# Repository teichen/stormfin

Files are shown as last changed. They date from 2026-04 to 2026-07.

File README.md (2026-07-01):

# StormFin
underactuated fish finder

# ChibbComm
raspberry pi land communicator and StormFin controller

## motivation
avoiding $1500+ Garbin LiveScope Plus \
avoiding $2000+ per acoustic modem \
current state of the art is forward facing sonar \
steerable transducer on trolling motor, 20 deg sonar beam, 100 ft range \
proposal - AUV tracking

## StormFin microcontroller and comms
Adafruit METRO 328 / Arduino Nano Complementary Filtering on-board \
Embedded EKF would require STM32H7 (for example), CMSIS-DSP library, etc. \
Arduino Due (84MHz 32-bit ARM Cortex-M3 processor, 96KB SRAM) would struggle with EKF \
Acoustic modem (design described below)

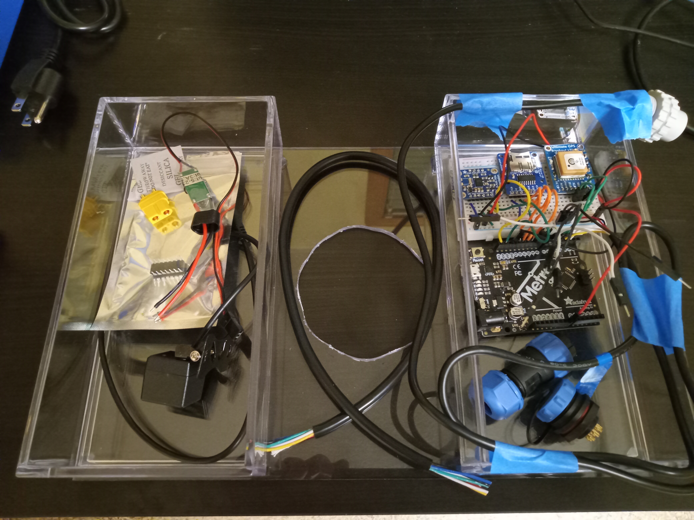
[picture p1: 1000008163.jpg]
prototyping1

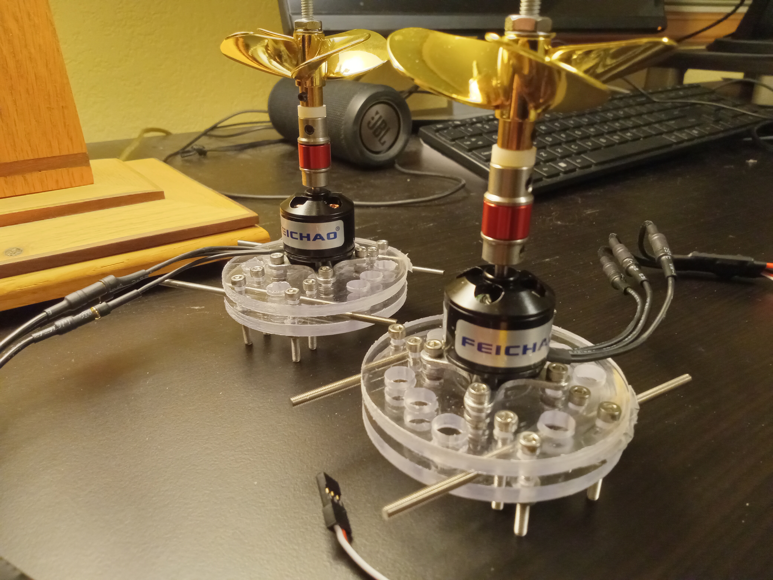
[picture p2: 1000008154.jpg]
prototyping0


## ChibComm microcontroller and comms
Raspberry Pi (3) Model B+ \
WhatsApp for communication with shoreline \
Acoustic modem (design described below) \
GNU Radio for signal processing (freq shift keying and phase shift keying)

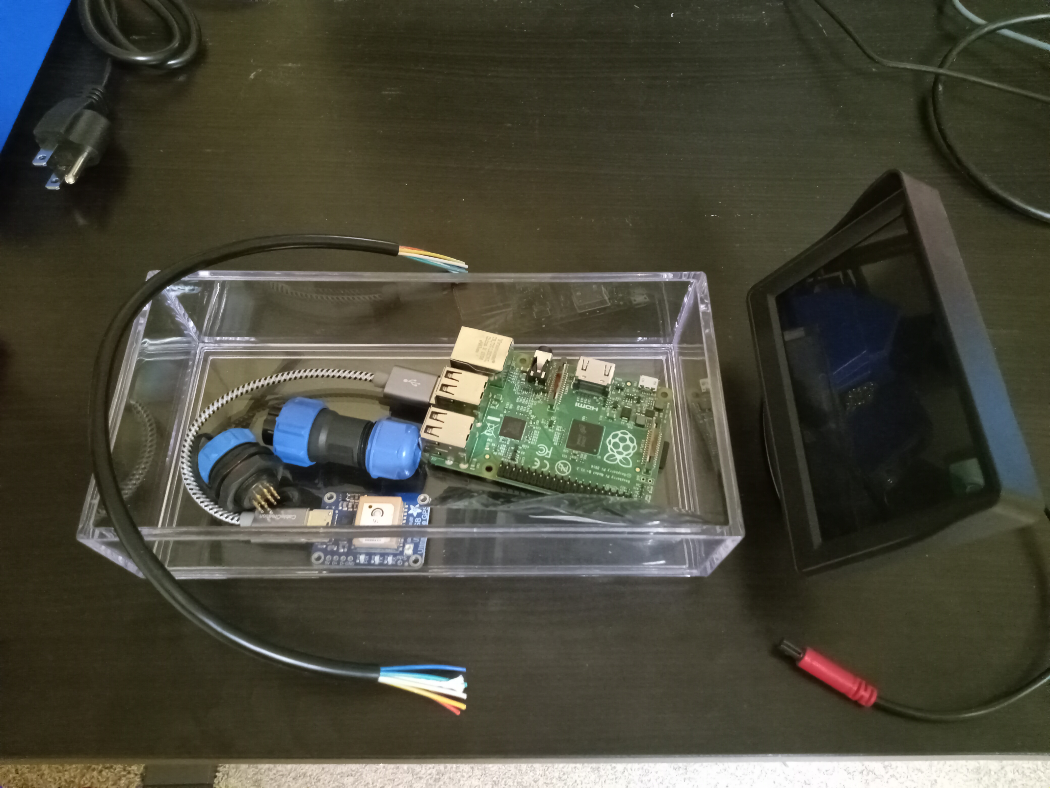
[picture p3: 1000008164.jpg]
prototyping2


## design sketch

## bill of materials
    1. SP17 IP68 10 pin waterproof connectors
    2. A2212 930KV brushless motors
    3. 55mID 60mmOD 4 blade propellers
    4. DFRobot IP68 6m UART ultrasonic sensor
    5. BNO055 IMU sensor
    6. ATmega 328P
    7. 3S LiPo Battery (11.1V) with charger
    8. GLONASS + GPS PA1616D - 99 channel w/ 10Hz
    9. ESC (20A) with BEC speed controller
    10. 64MB microSD
    11. Raspberry Pi Model B+
    12. UBEC DC/DC Step-Down (Buck) Converter - 5V @ 3A output
    13. B6AC 80W Balance Charger
    14. JLI PZ001 cylindircal ceramic pizeo electric transducer
    15. Differential Op-Amp
    16. LM311 Comparitor
    17. Class AB+D Amplifier
    18. JLI P48 Hi Z high impedance buffer (includes OPA1642 dual JFET amplifier embedded)
    19. bandpass (Sallen-Key) filter
    20. MCP3008 Analog-to-Digital Converter (ADC)

## powering/wiring StormFin and ChibbComm
    1. 11.1V 2.2A 25C LiPo battery (a) provides 610W continuous - two A2212 930KV motors draw 150W each
    2. 12V to 5V buck converter and single A2212 930KV motor on LiPo (b)
    3. StormFin IP68 10 pin to ChibbComm - 30m ethernet CAT6 unshielded w/ durable insulation
    4. Arduino to IP68 10 pin - 1m 10 core 24 AWG
    5. ESC to Arduino - 3 wire 60 core 22 AWG
    6. LiPo to ESC - 14 AWG silicon insulated stranded tinned copper
    7. LiPo to buck converter - 14 AWG silicon insulated stranded tinned copper
    8. LiPo to 12V camera - 14 AWG silicon insulated stranded tinned copper
    9. ChibbComm 12 camera draws 30W

## acoustic modem
```mermaid
flowchart TD
    A[transducer PZT] --> B[transceiver]
    B --- C[transmitter]
    B --- D[receiver]
    C --- E(precondition with differential Op-Amp)
    C --- F(Controller/Comparitor LM311)
    C --- G(Class AB amplifier, low noise high resolution)
    C --- H(Class D amplifier, high power long range)
    D --- I(high impedance buffer)
    D --- J(low pass active Sallen-Key filter)
    D --- K(high pass active Sallen-Key filter)
```
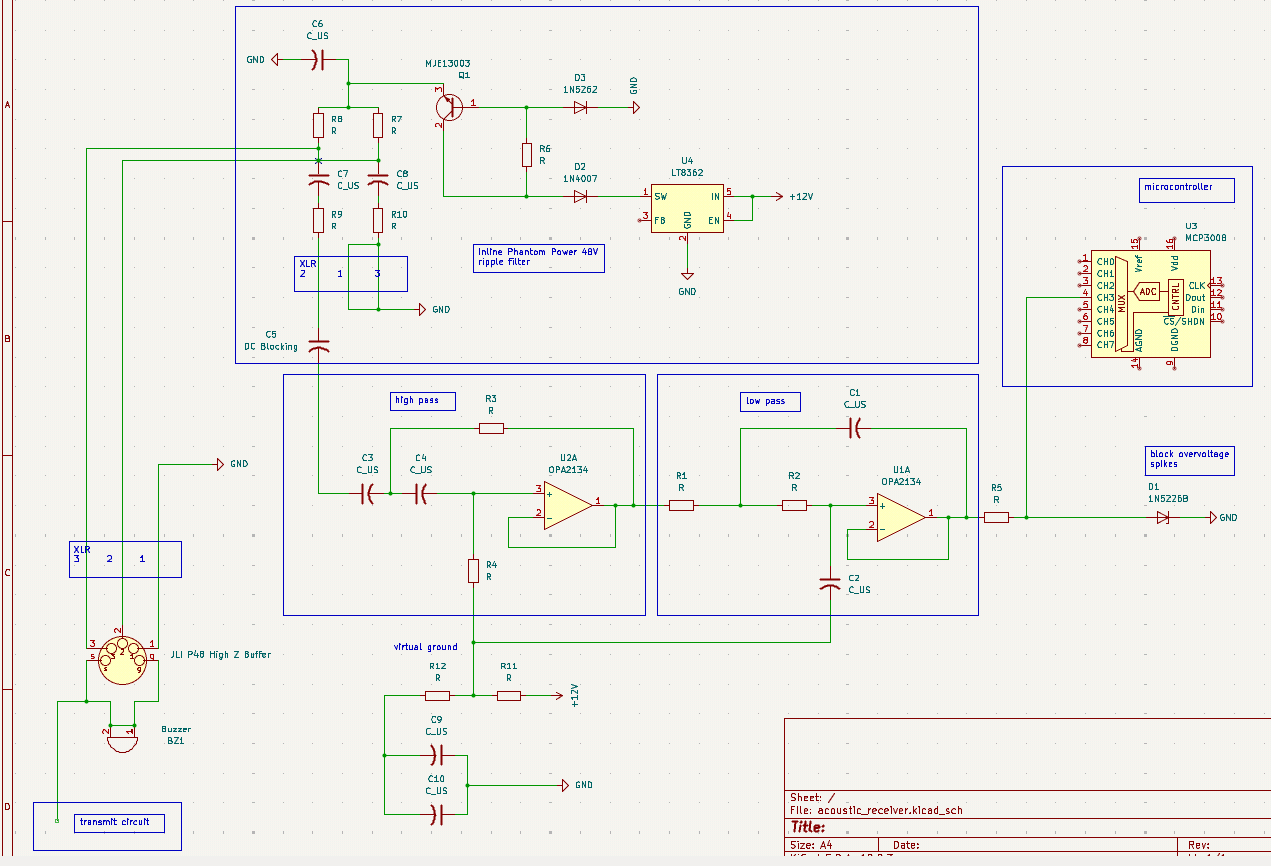
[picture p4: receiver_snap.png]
prototyping3

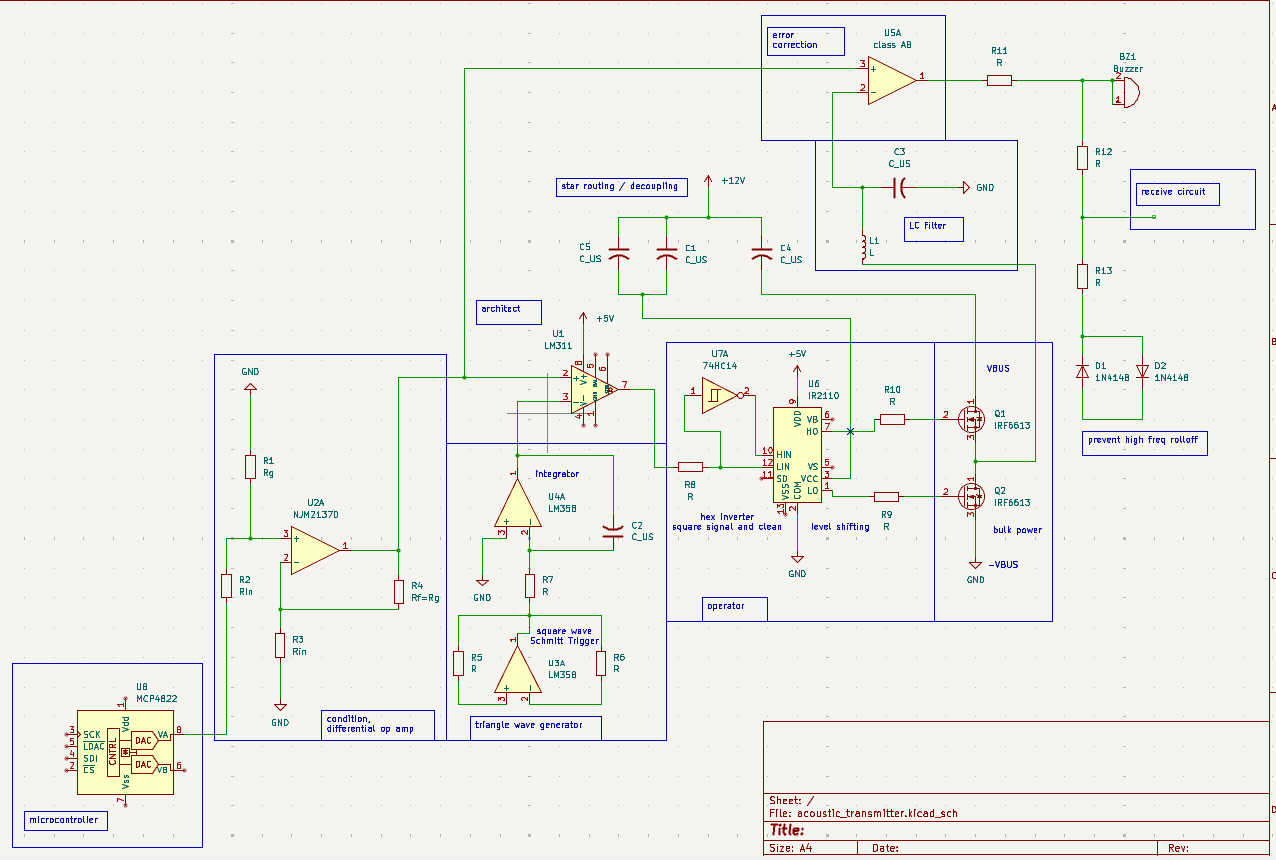
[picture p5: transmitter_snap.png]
prototyping4


## software overview
```mermaid
classDiagram
    Controller ..> Filter
    Controller ..> Sensors
    Controller ..> Thrusters
    Controller ..> Collocation
    Controller ..> Utilities
    Controller ..> DataStore
    Filter ..> Utilities
    Filter ..> GSLWrappers
    Filter ..> LaminarModel
    Filter : +void initialize_state()
    Filter : +void process(double, double*, double*, double*, double*)
    Filter : +void estimate_measurements(double*, double*)
    Filter : +void update(double*)
    Sensors : +void qrot_pure(double*, double*)
    Sensors : +void body_to_nav(double*, double*, double*)
    Sensors : +void set_qrot(double*)
    Sensors : +void qrot_pure(double*, double*)
    Sensors : +void ultrasonic_distance(double)
    Thrusters : +void thrust_to_pwm(double*, double*)
    Collocation : +void optimal_thrust(double*, double*, int, double*)
    Utilities : 
    GSLWrappers : 
    DataStore : 
```

## test plan
    1. prototype
    2. grid test xy filtered position and orientation
    3. ultrasonic stop when target acquired
    4. ultrasonic circling thrust default
    5. ultrasonic stalk, throttle when target receeding
    6. submersible (no power)
    7. pool test
    8. lake test (laminar no current)
    9. river test (laminar current)

## TODO
    1. insufficient memory for iostream, stdlib explicitly included
    2. GSL for off-board EKF testing / validation
    3. use DMA (Direct Memory Access) for sensor inputs rather than analogRead()

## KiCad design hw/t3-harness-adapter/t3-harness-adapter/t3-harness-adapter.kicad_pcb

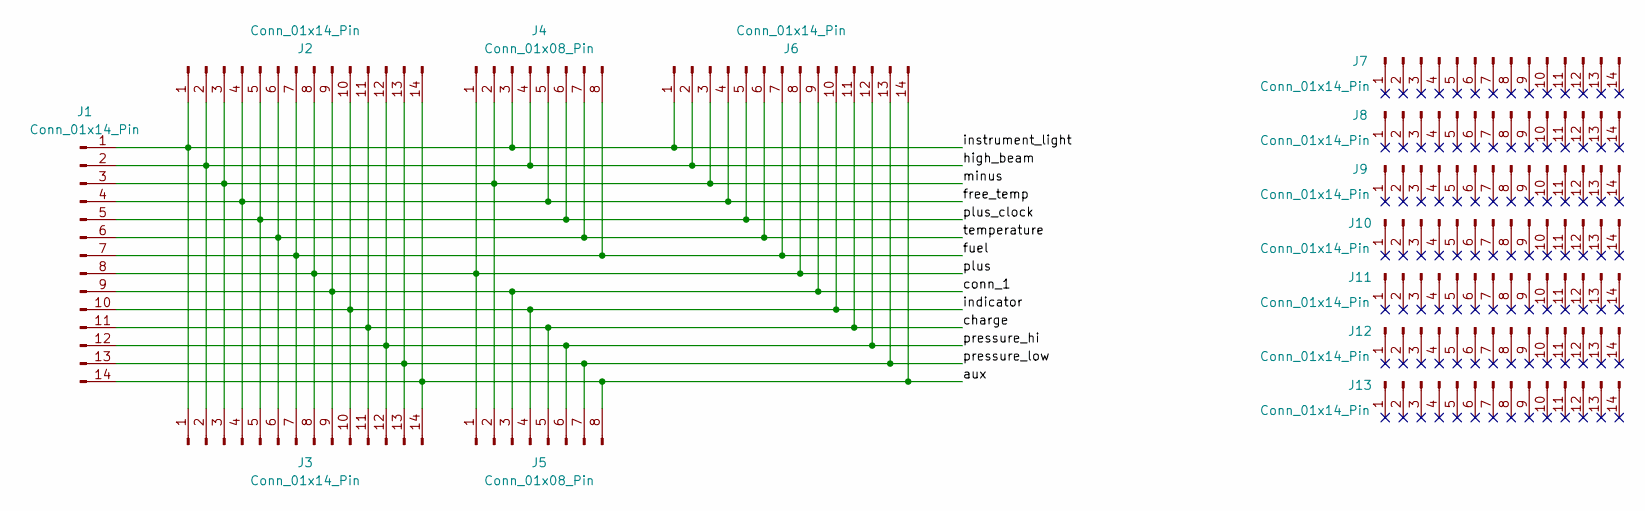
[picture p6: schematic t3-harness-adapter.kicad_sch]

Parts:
J1: Conn_01x14_Pin; t3-harness-edge
J2, J3, J6, J7, J8, J9, J10, J11, J12, J13: Conn_01x14_Pin; PinHeader_1x14_P2.54mm_Vertical
J4, J5: Conn_01x08_Pin; PinHeader_2x04_P2.54mm_Vertical

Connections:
/aux: J1.14, J2.14, J3.14, J5.8, J6.14
/charge: J1.11, J2.11, J3.11, J5.5, J6.11
/conn_1: J1.9, J2.9, J3.9, J5.3, J6.9
/free_temp: J1.4, J2.4, J3.4, J4.5, J6.4
/fuel: J1.7, J2.7, J3.7, J4.8, J6.7
/high_beam: J1.2, J2.2, J3.2, J4.4, J6.2
/indicator: J1.10, J2.10, J3.10, J5.4, J6.10
/instrument_light: J1.1, J2.1, J3.1, J4.3, J6.1
/minus: J1.3, J2.3, J3.3, J4.2, J5.2, J6.3
/plus: J1.8, J2.8, J3.8, J4.1, J5.1, J6.8
/plus_clock: J1.5, J2.5, J3.5, J4.6, J6.5
/pressure_hi: J1.12, J2.12, J3.12, J5.6, J6.12
/pressure_low: J1.13, J2.13, J3.13, J5.7, J6.13
/temperature: J1.6, J2.6, J3.6, J4.7, J6.6

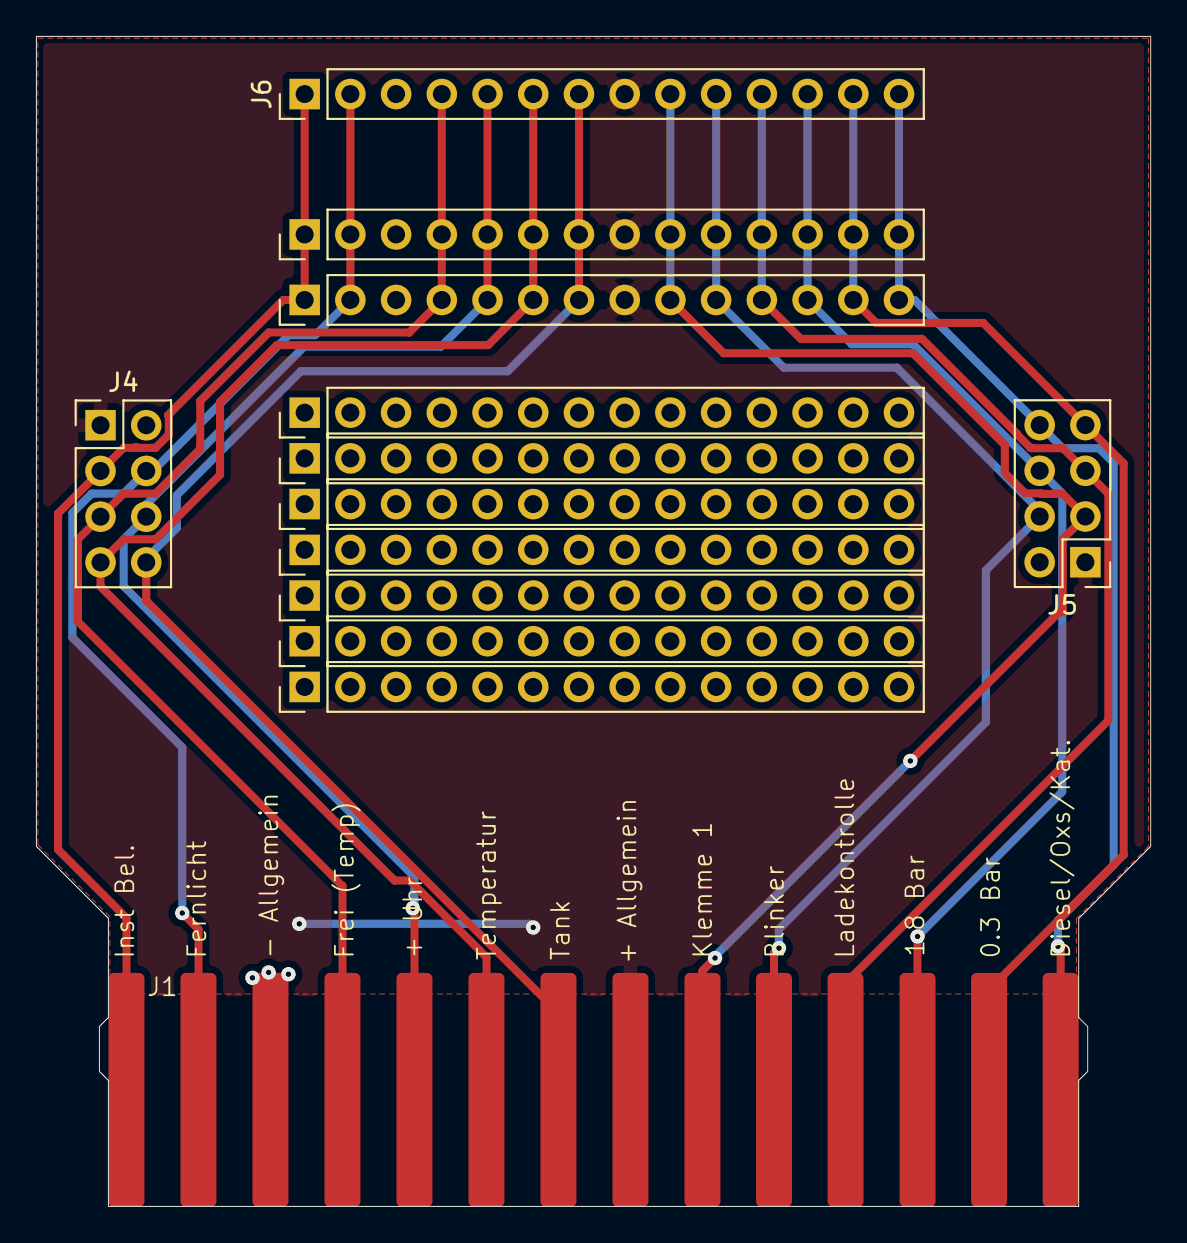
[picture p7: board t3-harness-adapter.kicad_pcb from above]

Board: 2 copper layers, 61.9 x 65.0 mm, 13 parts (0 on the bottom side), 14 nets.

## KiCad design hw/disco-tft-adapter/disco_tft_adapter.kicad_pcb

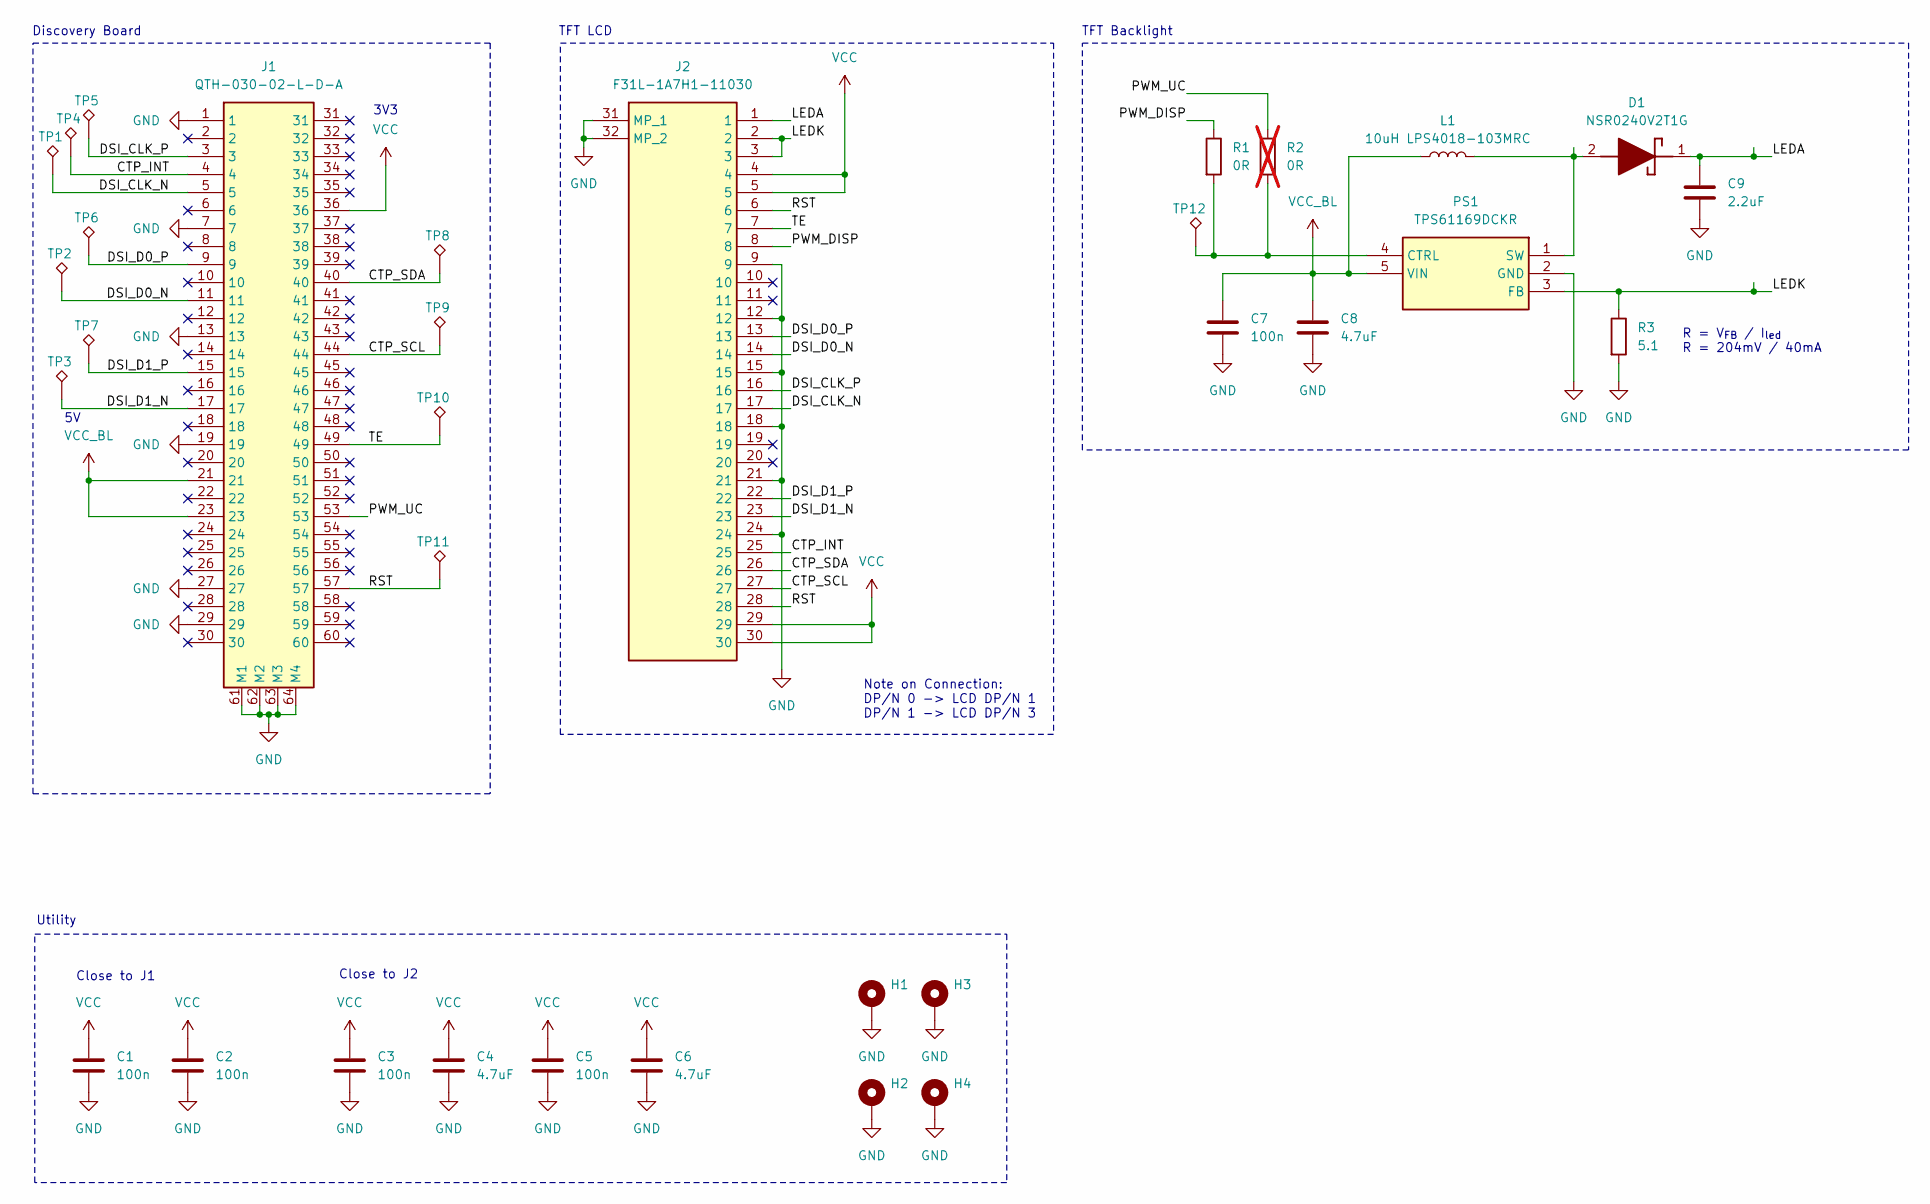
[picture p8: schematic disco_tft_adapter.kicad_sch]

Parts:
C1, C2, C3, C5, C7: 100n; C_0603_1608Metric; Mouser Part Number 603-C0603MRY5V9BB104
C4, C6, C8: 4.7uF; C_0805_2012Metric_Pad1.18x1.45mm_HandSolder; Mouser Part Number 581-08055D475KAT2A
C9: 2.2uF; C_0805_2012Metric_Pad1.18x1.45mm_HandSolder; Mouser Part Number 603-CC805KKX5R9BB225
D1: NSR0240V2T1G; SODFL1608X70N; Mouser Part Number 863-NSR0240V2T1G
H1, H2, H3, H4: MountingHole_Pad; MountingHole_4.5mm_Pad_TopBottom
J1: QTH-030-02-L-D-A; QTH-030-XX-Y-D-A; Mouser Part Number 200-QTH03002LDA
J2: F31L-1A7H1-11030; F31L1A7H111030; Mouser Part Number 649-F31L-1A7H1-11030
L1: 10uH LPS4018-103MRC; L_Coilcraft_1515SQ-47N; Mouser Part Number 994-LPS4018-103MRC
PS1: TPS61169DCKR; SOT65P210X110-5N; Mouser Part Number 595-TPS61169DCKR
R1: 0R; R_0603_1608Metric; Mouser Part Number 71-RCA06030000ZSEASR
R2: 0R; R_0603_1608Metric; Mouser Part Number 71-RCA06030000ZSEASR; not fitted
R3: 5.1; R_1206_3216Metric; Mouser Part Number 71-CRCW12065R10FKEA
TP1, TP2, TP3, TP4, TP5, TP6, TP7, TP8, TP9, TP10, TP11, TP12: TestPoint_Alt; TestPoint_TP_D0.5mm

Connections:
/CTP_INT: J1.4, J2.25, TP4.1 (1_1)
/CTP_SCL: J1.44, J2.27, TP9.1 (1_1)
/CTP_SDA: J1.40, J2.26, TP8.1 (1_1)
/DSI_CLK_N: J1.5, J2.17, TP1.1 (1_1)
/DSI_CLK_P: J1.3, J2.16, TP5.1 (1_1)
/DSI_D0_N: J1.11, J2.14, TP2.1 (1_1)
/DSI_D0_P: J1.9, J2.13, TP6.1 (1_1)
/DSI_D1_N: J1.17, J2.23, TP3.1 (1_1)
/DSI_D1_P: J1.15, J2.22, TP7.1 (1_1)
/LEDA: C9.1, D1.1 (K), J2.1
/LEDK: J2.2, J2.3, PS1.3 (FB), R3.1
/PWM_DISP: J2.8, R1.1
/PWM_UC: J1.53, R2.1
/RST: J1.57, J2.6, J2.28, TP11.1 (1_1)
/TE: J1.49, J2.7, TP10.1 (1_1)
GND: C1.2, C2.2, C3.2, C4.2, C5.2, C6.2, C7.2, C8.2, C9.2, H1.1 (1_1), H2.1 (1_1), H3.1 (1_1), H4.1 (1_1), J1.1, J1.7, J1.13, J1.19, J1.27, J1.29, J1.61 (M1), J1.62 (M2), J1.63 (M3), J1.64 (M4), J2.9, J2.12, J2.15, J2.18, J2.21, J2.24, J2.31 (MP_1), J2.32 (MP_2), PS1.2 (GND), R3.2
unnamed: D1.2 (A), L1.2, PS1.1 (SW)
unnamed: PS1.4 (CTRL), R1.2, R2.2, TP12.1 (1_1)
VCC: C1.1, C2.1, C3.1, C4.1, C5.1, C6.1, J1.36, J2.4, J2.5, J2.29, J2.30
VCC_BL: C7.1, C8.1, J1.21, J1.23, L1.1, PS1.5 (VIN)

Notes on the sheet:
3V3
Close to J1
Discovery Board
Close to J2
TFT Backlight
R = V_{FB} / I_{led} R = 204mV / 40mA
TFT LCD
Note on Connection: DP/N 0 -> LCD DP/N 1 DP/N 1 -> LCD DP/N 3
Utility

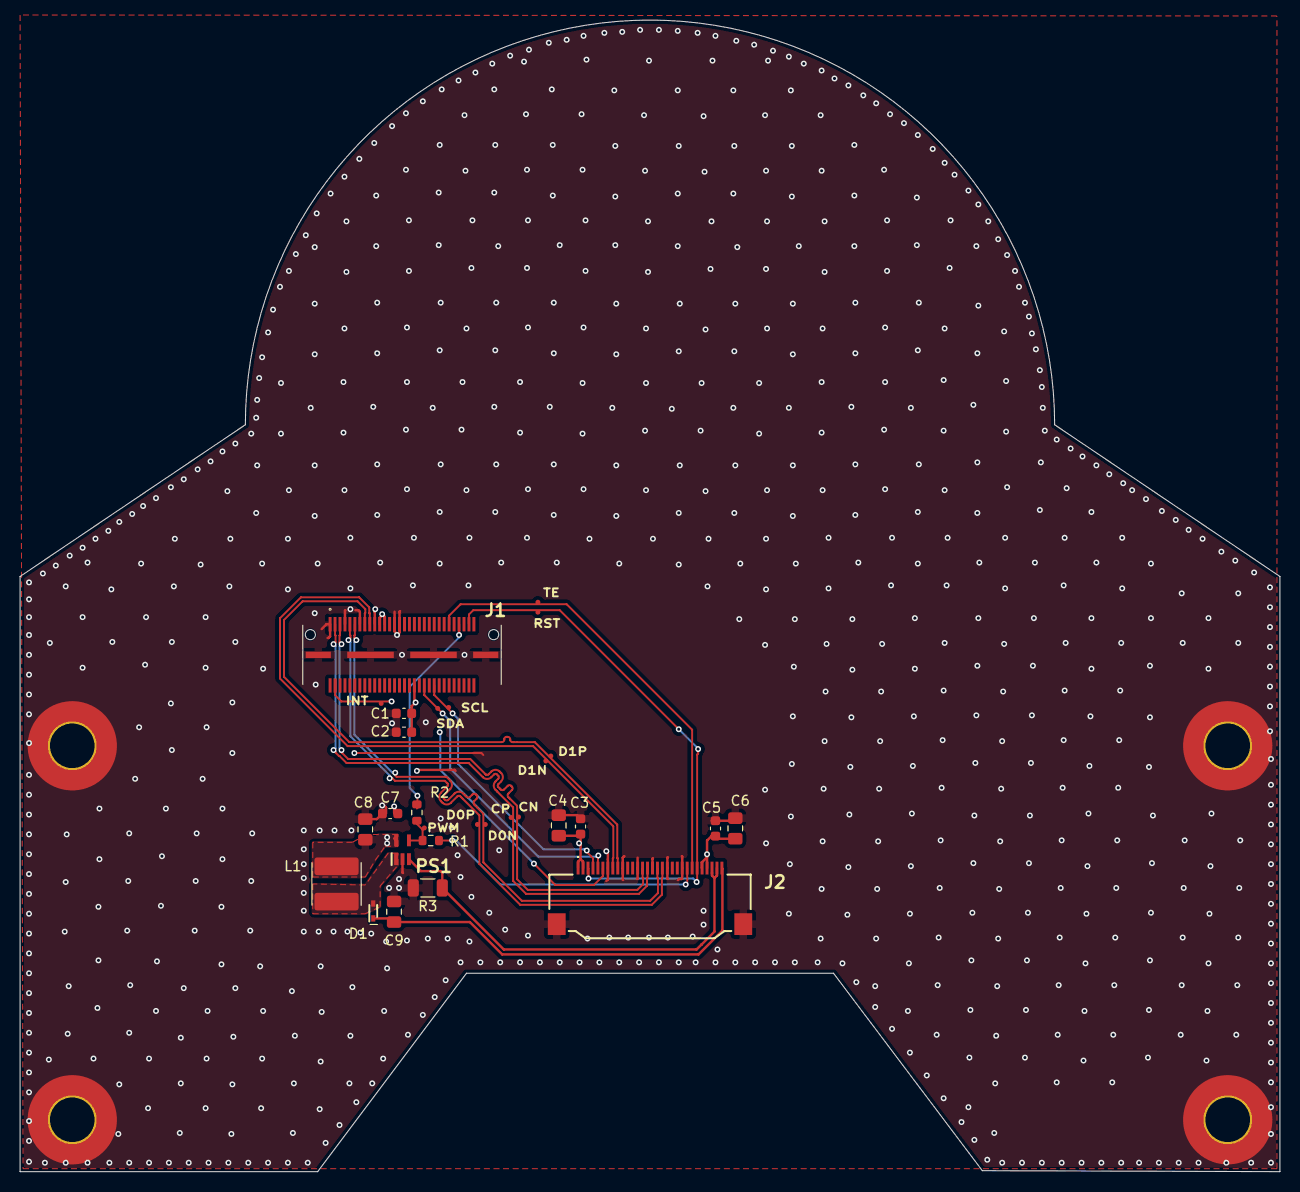
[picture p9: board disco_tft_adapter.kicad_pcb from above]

Board: 4 copper layers, 127.0 x 116.1 mm, 33 parts (0 on the bottom side), 20 nets.

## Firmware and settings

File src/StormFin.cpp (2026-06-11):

#include <iostream>
#include <cmath>
#include <cstdlib>
#include "MockData.h"
#include "Controller.h"
#include "Collocation.h"
#include "LaminarModel.h"
#include "Sensors.h"
#include "Acoustics.h"
#include "Thrusters.h"
#include "DataStore.h"
#include <gperftools/profiler.h>
#include <chrono>

#define COM 0x55

/*
TODO: automate main.cpp->arduino main.ino.cpp

#include <Arduino.h>
#include <Wire.h>
#include <Adafruit_Sensor.h>
#include <Adafruit_BNO055.h>
#include <utility/imumaths.h>
#include <Servo.h>
#include <SPI.h>
#include <SD.h>

//Set the delay between fresh samples
uint16_t BNO055_SAMPLERATE_DELAY_MS = 100;

// Check I2C device address and correct line below (by default address is 0x29 or 0x28)
//                                   id, address
Adafruit_BNO055 bno = Adafruit_BNO055(55, 0x28, &Wire);

SoftwareSerial ultrasonicSerial(2, 3); // IP68 UART ultrasonic
unsigned char ultrasonic_data[4];

Servo ESC;

const int CSPin = 10;          // MCP3008 Chip Select Pin

// Digital Bandpass Filter variables
// exponential moving average parameterization
float EMA_a_low = 0.3;         // Low-pass filter alpha (adjust for upper cutoff)
float EMA_a_high = 0.5;        // High-pass filter alpha (adjust for lower cutoff)
int EMA_S_low = 0;             // Low-pass filter state
int EMA_S_high = 0;            // High-pass filter state

*/

static int STOP = 0;
static int DIVE = 1;
static int SURFACE = 2;
static int SURVEILLANCE = 3;
static int STALK = 4;
static int COMMUNICATE = 5;

const int chipSelect = 10;
string data_string = "";

Sensors sensors; // utility functions, e.g. ref frame rotations
Thrusters thrusters; // utility functions, e.g. effective thrust inputs
Controller controller; // sensor fusion, estimation, navigation
DataStore datastore; // csv formatting
LaminarModel model;
Collocation coll;
MockData mock_data;
Acoustics acoustics;

using namespace std::chrono_literals;
using SystemTimePoint = std::chrono::system_clock::time_point;

auto dt1s = 1s;
double dt = 0.0;

int nav_state = DIVE;
SystemTimePoint t0 = std::chrono::system_clock::now();
SystemTimePoint t = t0;
SystemTimePoint t_stop = t0;

SystemTimePoint t_dive = t0;
SystemTimePoint t_surface = t0;
SystemTimePoint t_comms_off = t0;
SystemTimePoint t_comms_on = t0;

int i,j;

double omega_nav[4];
double mag_nav[4];
double a_nav[4];

double d0 = 0.0; // previous distance [=] cm, placeholder
double d_stop = d0; // stop distance

int pwm[3];
double u[3]; // thrust: L forward/reverse, R forward/reverse, Vertical (dive/surface)
double u_saved[3];

using namespace std;

/*
// Function to read a specific channel (0-7) from MCP3008
int readMCP3008(int channel) {
    int adcValue = 0;

    // Configure SPI communication settings
    SPI.beginTransaction(SPISettings(1000000, MSBFIRST, SPI_MODE0));

    digitalWrite(CSPin, LOW); // Select MCP3008

    // Send start bit + single-ended bit + channel config (bits 3-0)
    SPI.transfer(0x01); // Start bit
    byte commandBytes = ((channel + 8) << 4);
    byte msb = SPI.transfer(commandBytes);
    byte lsb = SPI.transfer(0x00);

    digitalWrite(CSPin, HIGH); // Deselect MCP3008
    SPI.endTransaction();

    // Combine the response bits into a 10-bit integer
    adcValue = ((msb & 0x03) << 8) | lsb;

    return adcValue;
}
*/

int main()
{
    ProfilerStart("/tmp/prof.out"); // memory profiler

    double x[model.n_s];
    double s2[model.n_s * model.n_s];
    double z[model.n_m];

    // thrust setpoints
    int n_t = 100;
    double t_set[n_t];
    double u_set[n_t * 3];
    for (i=0; i<n_t; i++)
    {
        t_set[i] = 0.0;
        u_set[i*3 + 0] = 0.0;
        u_set[i*3 + 1] = 0.0;
        u_set[i*3 + 2] = 0.0;
    }

    int idx_set;
   
    model.init_state(x);
    model.init_covariance(s2);
    /*
    // arduino setup()
    Serial.begin(115200); // BNO055

    sensors_event_t orientationData , angVelocityData , linearAccelData, magnetometerData, accelerometerData, gravityData;
    uint8_t system, gyro, accel, mag = 0;

    ESC.attach(9, 1000, 2000); // ESC connected to PIN 9

    // MCP3008 ADC and SPI
    // acoustic signal from a piezoelectric element alternates between positive and negative voltages
    // high-impedance buffer circuit applies a DC bias and raises the AC waveform so it never drops below 0V
    pinMode(CSPin, OUTPUT);
    digitalWrite(CSPin, HIGH);   // Disable device initially
    SPI.begin();
    Serial.begin(115200);

    // Initialize filter states with first reading
    int initialReading = readMCP3008(0);
    EMA_S_low = initialReading;
    EMA_S_high = initialReading;
    */
    pwm[0] = 0.0;
    pwm[1] = 0.0;
    pwm[2] = 0.0;
    u[0] = 0.0;
    u[1] = 0.0;
    u[2] = 0.0;
    u_saved[0] = u[0];
    u_saved[1] = u[1];
    u_saved[2] = u[2];

    // arduino loop()
    while (true) {
        /*
           (0) process acoustic data
           (1) process sensor data
           (2) determine operating state
               (a) ROV manual
               (b) circling surveilance
               (c) target acquisition - stalking
               (d) target acquisition - abandon to surface
           (2) run estimation and navigation routines
           (3) adjust thrust
        */

        /* (0) process acoustic data
        int rawValue = readMCP3008(0); // Read acoustic signal from CH0

        // Bandpass implementation (Subtract Low-pass from High-pass)
        EMA_S_low = (EMA_a_low * rawValue) + ((1 - EMA_a_low) * EMA_S_low);
        EMA_S_high = (EMA_a_high * rawValue) + ((1 - EMA_a_high) * EMA_S_high);

        int bandpassResult = EMA_S_high - EMA_S_low;
        */

        // (1) process sensor data
        mock_data.request_data(nav_state);

        controller.qrot_imu_data(mock_data.q, mock_data.omega_body, mock_data.mag_body, mock_data.a_body,
                              omega_nav, mag_nav, a_nav);

        z[model.mi_omega_x] = omega_nav[1];
        z[model.mi_omega_y] = omega_nav[2];
        z[model.mi_omega_z] = omega_nav[3];
        z[model.mi_a_x] = a_nav[1];
        z[model.mi_a_y] = a_nav[2];
        z[model.mi_a_z] = a_nav[3];
        z[model.mi_x] = mock_data.longitude;
        z[model.mi_y] = mock_data.latitude;
        z[model.mi_v_x] = mock_data.speed * std::cos(mock_data.gps_angle);
        z[model.mi_v_y] = mock_data.speed * std::sin(mock_data.gps_angle);
        z[model.mi_b_x] = mag_nav[1];
        z[model.mi_b_y] = mag_nav[2];
        z[model.mi_b_z] = mag_nav[3];

        // use extended Kalman filter to get best estimate for d
        // handle IMU, GPS, ultrasonic data as measurements with nonzero uncertainty
        SystemTimePoint t = std::chrono::system_clock::now();
        dt = (t - t0) / dt1s;

        controller.process_data(dt, x, s2, u, z);

        controller.update_nav_state(nav_state, t, t_comms_off, t_comms_on, t_surface, t_dive,
                                    mock_data.d, mock_data.q, idx_set, t_set, n_t, u_set, u_saved,
                                    d_stop, t_stop, d0);

        thrusters.thrust_state(nav_state, u_set, idx_set, u);
        if (nav_state == STOP){
            // save off last thrust configuration
            u_saved[0] = u[0];
            u_saved[1] = u[1];
            u_saved[2] = u[2];
        }

        thrusters.thrust_to_pwm(u, pwm);
        // ESC.writeMicroseconds(pwm);
        // delay(100);

        d0 = mock_data.d;
        t0 = t;

        /* TODO: data logging
        File dataFile = SD.open("datalog.txt", FILE_WRITE);

        // if the file is available, write to it:
        if (dataFile) {
            dataFile.println(dataString);
            dataFile.close();
            // print to the serial port too:
            Serial.println(dataString);
        }
        // if the file isn't open, pop up an error:
        else {
            Serial.println("error opening datalog.txt");
        }
        */

        break; // for testing
    }

    ProfilerStop();

    return 0;
}

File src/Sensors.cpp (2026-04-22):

#include <stdlib.h>
#include "Sensors.h"

using namespace std;

Sensors::Sensors()
{
    /* DFRobot IP68 6m UART ultrasonic sensor, ~30ft depth, 20ft distance capacity
       TTL Serial (UART) protocol with Arduino
       VIN-5V, D2 (white), D3 (yellow), GND-GND
       transducer is engineered for the density and sound speed of water
       echoTime
       distance = echoTime * 0.0343 / 2.

       BNO055 strapdown IMU (MEMS)
       16bit gyro, 14bit accelerometer
       inter-integrated circuit (I2C) protocol with Arduino
       SDA serial data, SCL serial clock, 115200 baud
       quaternions, q, at 100 Hz
       angular velocity, omega, at 100 Hz
       acceleration, a [=] m / s**2, at 100 Hz
       gravity, g [=] m / s**2, without movement, at 100 Hz

       GLONASS + GPS PA1616D - 99 channel with 10 Hz update
       TTL Serial (UART) protocol with Arduino
       9600 baud
       VIN-5V, RX-7, TX-8, GND-GND
       fix, latitude, longitude, speed
    */
    mem_test = false;
    initarrays();

}

void Sensors::set_qrot(double* q)
{
    // body to inertial (NAV) frame rotation
    m[0] = 1.0 - 2.0 * (q[2] * q[2]) - 2.0 * (q[3] * q[3]);
    m[1] = 2.0 * (q[1] * q[2] - q[0] * q[3]);
    m[2] = 2.0 * (q[1] * q[3] + q[0] * q[2]);
    m[3] = 2.0 * (q[1] * q[2] + q[0] * q[3]);
    m[4] = 1.0 - 2.0 * (q[1] * q[1]) - 2.0 * (q[3] * q[3]);
    m[5] = 2.0 * (q[2] * q[3] - q[0] * q[1]);
    m[6] = 2.0 * (q[1] * q[3] - q[0] * q[2]);
    m[7] = 2.0 * (q[2] * q[3] + q[0] * q[1]);
    m[8] = 1.0 - 2.0 * (q[1] * q[1]) - 2.0 * (q[2] * q[2]);
}


void Sensors::qrot_pure(double* q, double* a)
{
    // pure quarternion rotation, a = q x a x q^-1
    double a_rot[4];

    // q = (q[0], qv) where qv = q[1:3]
    // a = (a[0], av) where av = a[1:3]
    // q x a = (q[0] * a[0] - qv dot av, q[0] * av + a[0] * qv + qv cross av)
    double qa[4];
    qa[0] = q[0] * a[0] - (q[1] * a[1] + q[2] * a[2] + q[3] * a[3]);
    qa[1] = q[0] * a[1] + a[0] * q[1] + (q[2] * a[3] - q[3] * a[2]);
    qa[2] = q[0] * a[2] + a[0] * q[2] + (q[3] * a[1] - q[1] * a[3]);
    qa[3] = q[0] * a[3] + a[0] * q[3] + (q[1] * a[2] - q[2] * a[1]);

    // q* = q^-1 = (q[0], -v)
    a_rot[0] = qa[0] * q[0] + (qa[1] * q[1] + qa[2] * q[2] + qa[3] * q[3]);
    a_rot[1] = -qa[0] * q[1] + q[0] * qa[1] - (qa[2] * q[3] - qa[3] * q[2]);
    a_rot[2] = -qa[0] * q[2] + q[0] * qa[2] - (qa[3] * q[1] - qa[1] * q[3]);
    a_rot[3] = -qa[0] * q[3] + q[0] * qa[3] - (qa[1] * q[2] - qa[2] * q[1]);

    int i;
    for (i=0; i<4; i++)
    {
        a[i] = a_rot[i];
    }
}

void Sensors::body_to_nav(double* q, double* r_body, double* r_nav)
{
    set_qrot(q);

    int i,j;
    for (i=0; i<3; i++)
    {
        r_nav[i] = 0.0;
        for (j=0; j<3; j++)
        {
            r_nav[i] += m[i*3 + j] * r_body[j];
        }
    }
}

void Sensors::ultrasonic_distance(double distance)
{
    /* scale the distance and use drift in orientation to predict center of mass
    */
    distance /= 10; // units of cm
}

void Sensors::initarrays()
{
    m    = (double*) calloc (9, sizeof(double));
    mem_test  = true;
}

Sensors::~Sensors()
{
    if(mem_test==true)
    {
    delete [] m;
    }
}

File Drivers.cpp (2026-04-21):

#include <stdlib.h>
#include "Drivers.h"

using namespace std;

Drivers::Drivers()
{
    /* A2212 930KV brushless motors
       60mm blade propellers
       electronic speed controller (ESC), pulse width modulation (PWM) protocol with Arduino
       calibrate effective thrust (accounting for water drag)
    */
}

void Drivers::thrust_to_pwm(double* u, double* pwm)
{
    /* provided a thrust, u [=] N, estimate a PWM (mapped) in microseconds
       u ~ c * PWM ** 2 where c is a coefficient of thrust
       pwm ~ 1500 microsec for warm up, 0 <= pwm <= 2000 microsec
    */
}

Drivers::~Drivers()
{
}

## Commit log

2026-04-17 remove arduino and add missing iostream headers
    [Drivers.cpp, Sensors.cpp]
2026-04-19 adding model and filter linalg
2026-04-19 sensors drivers docstrings
2026-04-20 FIX TEST quarternion rotations
    [Sensors.cpp, controller_test.cpp]
2026-04-20 FIX pure quarternion rotation
    [Sensors.cpp, controller_test.cpp]
2026-04-20 read in gyro data
2026-04-21 setup ip68 uart ultrasonic for arduino
2026-04-21 sketch collocation and drivers
2026-04-21 rename thrusters class
2026-04-21 test plan and bom
2026-04-22 prototyping microcontroller board
2026-04-22 add simple low thrust collocation absent sensor data
2026-04-22 ultrasonic distance to sensors
2026-04-22 thrust to pwm
2026-04-22 work on controller filter structure
2026-04-23 add ESC with BEC
2026-04-23 thrust based on nav states
2026-04-23 left right vertical thrust
2026-04-24 pass sensor data to controller
2026-04-24 add gyro drift and accel bias to estimate
2026-04-24 passing thrust to state dynamics
2026-04-27 FIX filter process with arbitrary start
2026-04-27 FIX filter process test with no sensor data
2026-04-28 TODO update filter with partial measurement data
2026-04-29 projected filter update for nonnan sensor data
2026-04-29 FIX filter update
2026-04-29 hack off gyro drift and accel bias from meas jac
2026-04-30 adding complementary filter for on-board algo
2026-05-01 add mag sensor data
2026-05-01 no mag sensor data in datastore
2026-05-03 work on complementary filter and gps velocities
2026-05-03 pass in imu mag sensor data
2026-05-04 complementary filter update
2026-05-04 FIX complementary filter nan handling with tests
2026-05-13 powering wiring README
2026-05-15 stronger gyro weight
2026-05-15 target acquisition, damped inertia, thrust setpoints via collocation
2026-05-15 qrot all imu data
2026-05-15 ultrasonic distance to MockData
2026-05-15 sequestered thrust state
2026-05-25 calibrate the esc
2026-06-10 forward facing sonar beam when no comms, GPS when surfacing
2026-06-17 acoustic modem pinouts
    [acoustic_receiver.kicad_pcb, acoustic_receiver.kicad_sch, acoustic_transmitter.kicad_pcb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]
